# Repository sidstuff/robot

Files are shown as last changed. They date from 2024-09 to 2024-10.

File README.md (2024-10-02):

# Obstacle avoiding robot

A common type is the micromouse, a small robot which tries to solve a maze. I.e., it tries to reach the center of a maze made up of a 16×16 grid of cells, each 180 mm square with walls 50 mm high.

## Usage

Clone the repo and open with KiCAD.

## Schematic

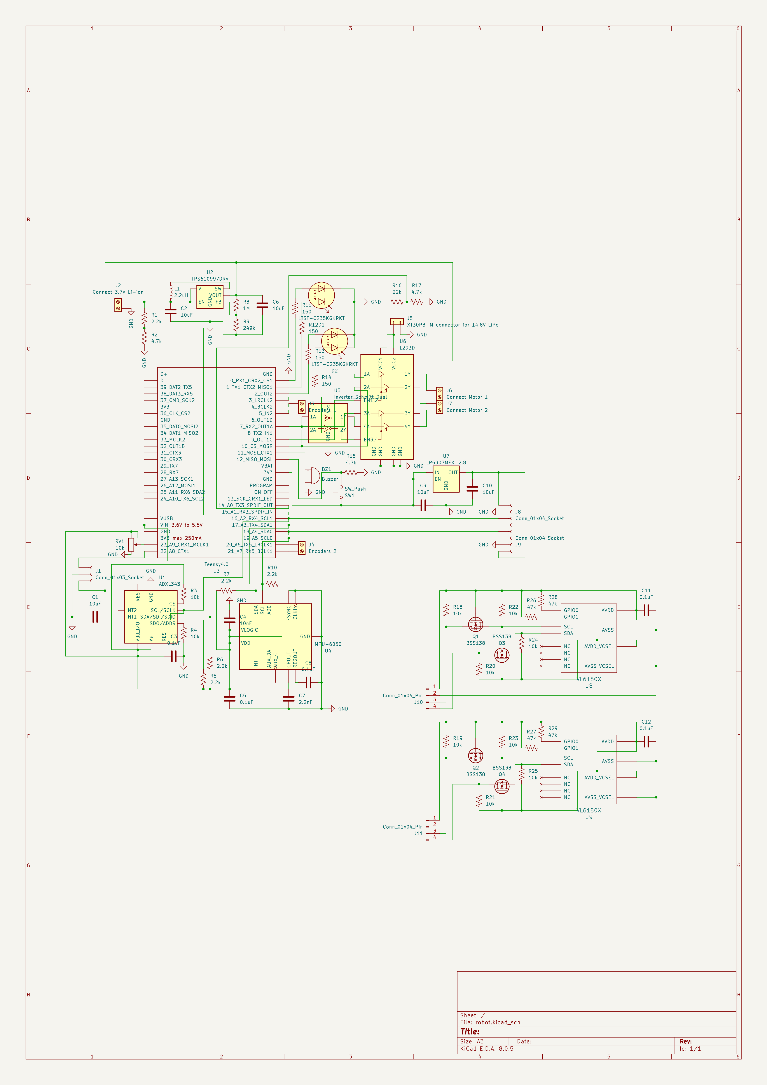
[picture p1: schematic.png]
Schematic


## Parts

While picking parts, ensure that the voltage/current/power ratings of componenets are not exceeded. Also, lithium cells have a nominal voltage of 3.7V (although it can go up to 4.2V when fully charged, and can be discharged until 3V), so their batteries are going to be multiples of the same.

### Microcontroller – Teensy 4.0

https://www.pjrc.com/store/teensy40.html

The Teensy 4.0 is compatible with the Arduino software, smaller than the Nano, and more powerful than the Giga (2x the CoreMark score). It needs a 5V supply voltage, so we'll use a 3.7V Li-ion battery with A TPS61099x 5V boost converter.

#### Why not older models?

> PJRC recommends use of Teensy 4.0 / 4.1 for new projects. We do not believe supply of chips for Teensy 3.x is likely to ever fully recover. These chips are made with 90 nm silicon process. Most of the world's semiconductor fabs are focusing on 45 nm or smaller, leaving limited supply for older chips. We anticipate the cost of these chips is likely to increase as the supply continues to dwindle.
>
> www.pjrc.com/store/teensylc.html

Thus we use the 4.x series to future-proof our design. The 4.0 is the smaller model of the series and is sufficient for our project.

### Motors – N20 gear motors, driven by the L293D

We will use the common N20 gear motor. To pick the specifications of the same, let's make use of this [Drive Motor Sizing Tool](https://community.robotshop.com/blog/show/drive-motor-sizing-tool)
```
Total mass: 210g                 When picking components, we should keep the total weight at or below this.
Number of drive motors: 2        Each of the rear wheels will have a sepaarte motor, turning will be achieved by driving them at different speeds.
Radius of drive wheel: 32.5 mm   Use 65 mm RC wheels
Robot velocity: 1.35 m/s         Micromice can run at over three meters per second, depending on the maze design.
Maximum incline: 0 deg           A simple maze solving robot doesn't need to worry about performance climbing inclines.
Supply voltage: 12 V             12V is the highest available voltage for the N20. A higher voltage means less current/charge is required for the same power/energy output. 
Desired acceleration: 4 m/s2     Micromice can run with forward acceleration and braking well over 1g.
Total efficiency: 40%            N20 motors have a maximum efficiency of around 0.4
```
```
Angular Velocity: 396.86 rpm
Torque: 0.34786 kgf-cm
Total Power: 1.4175 W
Maximum current: 118.13 mA
```
The [N20 motor rated for 12V 400RPM](https://robu.in/product/n20-12v-400-rpm-micro-metal-gear-motor) fulfils these requirements. It has a rated torque of 0.35 kg-cm. The recommendation for brushed DC motor operation is 25% or less of the stall current. The stall current for the above motor is 0.75 A, and the required current of 118.13 mA is less than 16% of it.

Make sure to buy the version with a [motor encoder](https://www.pololu.com/product/5215) and [its wires](https://www.pololu.com/product/4762) – it tells us how much the motor has rotated and thus the robot's speed as well as the distance travelled.

With these motors, we will use a pair of [65mm RC wheels](https://srituhobby.com/product/65mm-rubber-wheel-rc-model-tire).

On the [L293D motor driver](https://www.electronicscomp.com/l293d-dual-h-bridge-motor-driver-ic), there are two pins to control the direction of each motor as follows:
| IN1	| IN2 |	Spinning Direction |
| --- | --- | --- |
| LOW | LOW| Motor OFF |
| HIGH	| LOW | Forward |
| LOW | HIGH | Backward |
| HIGH	| HIGH |	Motor OFF |

The enable pin for each motor can be used to switch it on/off (as well as control the speed using PWM) so the `LOW,LOW` and `HIGH,HIGH` configurations are not needed. As for the remaining two, we can save two digital pins (one per motor) by using a logic inverter. Thus we use the Dual Schmitt-Trigger Inverter, but since we have a pin to spare, we end up using a digital pin for the inverter supply voltage (instead of the 3.3V pin) to simplify the connections.

The L293D will drop the motor supply voltage by ~2.6V, so we will use a 14.8V LiPo battery for the motors.

### Accelerometer – ADXL345

Calculating the position of the robot from the rotation of the motor is complicated by turns of the robot, and some slipping can mess up the entire calculation thereafter. Thus we make use of an accelerometer.

### Gyroscope - MPU6050

Similarly, a gyroscope tells us how many degrees the robot has turned.

<table><td><b>NOTE</b>: Both the ADXL345 and the MPU6050 are I2C devices and thus we use 2.2k pull-up resistors on the SDA and SCL connections because the Teensy's internal pull-up resistors are too weak.</td></table>

### Distance sensors

Note that distance sensors have a dead zone or blanking distance of say, x cm, beginning from the face of the sensor and extending outward, within which it cannot measure distances. One can simply position the sensor x cm inwards on the robot if they wish to measure distances in that zone.

#### Front - Sharp GP2Y0A41SK0F

https://www.pololu.com/product/2464

The GP2Y0A41SK0F is an IR sensor with a range of 4 – 30 cm. Considering the size of the robot and its enclosings, this is a good range within which to detect obstacles so the robot can decide if and how much to speed up, slow down, or stop, and can do so in time. A simple calculation is that if the robot is moving at its maximum speed of 1.35 m/s and has a maximum acceleration (deceleration in this case) of 4 m/s2, it can come to a stop within a distance of v²/2a = 22.8 cm.

This sensor draws current in large, short bursts, which is why we should (and do) place a 10 µF capacitor or larger across the 5V supply and ground, close to the sensor.

The sensor will be stuck to the front of the robot and a [3-Pin Female JST-PH Cable with male pins](https://www.pololu.com/product/1799) will be used to connect it to 0.1" female pins on our PCB.

#### Sides – VL6180X

https://www.pololu.com/product/2489

The sides of the robot will approach closer to walls and obstacles than the front, so a shorter minimum range is required. The VL6180X is a time-of-flight ranging sensor with a range of 1 – 20 cm (or 60 cm with reduced resolution), which is sufficient. It uses 2.8V logic, so we use the LP5907MFX-2.8 linear voltage regulator to convert 3.3V to 2.8V.

It is an I2C device, and we use 10k pull-up resistors on the SDA and SCL connections. Its I2C address will reset to 0x29 when powered off and on again, so for simplicity, we let the two chips have identical addresses and instead connect them to different SDA/SCL pins on the microcontroller.

Each chip (with its associated componenets) will be on a separate board that will be stuck to the side of the robot, and connected to the main PCB via common 0.1" pins and jumper cables.

### RG bicolor LEDs – LTST-C235KGKRKT

We use voltage dividers to supply a fraction of the two batteries' voltages to analog pins on the Teensy. Based on these, the microcontroller can make two corresponding bicolor LEDs display hues from green to yellow to red, to indicate the charge. An LED can blink red when the level is danngerously low, and blink green when its corresponding battery is done charging. The LED is rated for 20mA but the Teensy's pins have a limit of 10mA. The voltage supplied to the LED will always be 3.3V, the brightness will be controlled using PWM. The LED forward voltage is 2V. Thus the value of the current limiting resistor used should be at least (3.3−2)/0.01 = 130 ohms, so let's use a standard 150 ohm resistor.

### Buzzer – AI-3035-TWT-3V-R

We can have the buzzer buzz at different frequencies and beep at different delays to notify us of various things. Its rating of 3V,9mA is within the limits of the Teensy pin. For every doubling of distance, the sound level reduces by 6dB, so its volume of 100dB@10cm means that our buzzer will have a nicely audible volume of 60dB 10m away.

<table><td><b>TODO</b>: Due to laziness, the PCB currently uses KiCAD's standard 12x9.5mm buzzer footprint, which should be replaced with a custom but more accurate 30x20mm one – this means the PCB will be larger than it currently is.</td></table>

### Potentiometer – RK09K or similar

We'll use a 10k rotary potentiometer (vertical) with a knob to provide an analog voltage that indicates the speed at which we want the robot to move.

### Switches

We need two switches. First, an SPST rocker switch connected (not on the PCB) to the 3.7V battery to just switch on the circuitry, perhaps to check the working status of the components, battery level, etc. Then a normally open SPST Push button switch, like the MEC 5GTH935, to signal that the robot should start moving. Normally the Teensy pin is pulled down to ground, but when the switch is pressed, it momentarily becomes HIGH, and upon receiving this signal, the microcontroller starts the robot's motion.

### 2 Pin Screw Terminals – Xinya XY308-2P 2.54MM

In total, we require five [2 pin screw terminals](https://www.tme.com/in/en/details/xy308-2p-2.54-gn/pcb-terminal-blocks/xinya/xy308-2p-2-54mm-green) to connect various unterminated wires to the PCB.

### Batteries

| Part | Weight (g) | Voltage (V) | Current (mA) |
| --- | --- | --- | --- |
| 1 x Teensy 4.0 | 2.8 | 5 | 100 |
| 2 x N20 | 12 | 14.8 | 118 |
| 2 x wheels | 31 | - | - |
| 1 x L293D | 2.1 | 5 | 24 |
| 1 x ADXL345 | 0.03 | 3.3 | 0.04 |
| 1 x MPU6050 | 0.03 | 3.3 | 3.6 |
| 1 x GP2Y0A41SK0F | 3.5 | 5 | 12 |
| 2 x VL6180X (with LP5907MFX) | 0.03 | 3.3 | 25 |
| 2 x (LTST-C235KGKRKT + 150ohm) | 0.04 | 3.3 | 8.67 |
| 1 x AI-3035-TWT-3V-R | 12 | 3 | 9* |
| 1 x RK09K | 4.5 | 3.3 | 0.33 |
| 1 x Rocker Switch | 1.4 | 0 | - |
| 1 x 5GTH935 | 3 | 3.3 | 0.7* |
| 5 x XY308-2.54 | 0.5 | 0 | - |

`*` – current flows rarely

Adding all the weights, we get 112g. For the batteries, let's pick the [3.7V 3.7Wh 1000mAh LiPo](https://www.lithium-polymer-battery.net/lp543450-3-7v-1000mah-3-7wh-lithium-polymer-battery)  (20g) and the [Orange 14.8V 360mAh 25C 4S LiPo](https://robu.in/product/orange-360mah-4s-25c-14-8-v-lithium-polymer-battery-pack-li-po) (60g). This brings the weight up to 192g, but this is excluding the PCB material, wires, connectors, and small circuit elements. A PCB weighs a couple grams per square inch – see [custompcb.com/faq.php](https://custompcb.com/faq.php) – so the final weight should come out to around 210g.

The 14.8V Lipo is 25C, so can deliver a maximum current of 0.36Ah * 25h^(-1) = 9A, which is more than enough for our motors. They draw upto 2 * 118mA = 236 mA, so our battery will last 360mAh / 236 mA = 1.5h, if the robot was continuously running at full power, but in reality, will last longer.

The following diagram shows the flow of current from the 3.7V LiPo.
```
------------------------------------ 3.7V
               |
      301.2 mA (1114.5 mW)
               |
      ----------------------
      | TPS61099 (93% eff) |
      ----------------------
               |
---------------|-------------------- 5V
               |
      207.3 mA (1036.5 mW)
               |
      -------------------
      |                 |
      |              171.3 mA
      |                 |
 --------------  -------|------------------
 | 5V Devices |  |      |                 |
 --------------  |  ----------            |
      |          |  | Teensy |            |
      |          |  ----------            |
    36 mA        |   |      |             |
      |          |   |   ---|--- 3.3V     |
      |          | 100mA    |             |
      |          |   |   ---------------- |
      |          |   |   | 3.3V Devices | |
      |          |   |   ---------------- |
      |          |   |      |             |
      |          ----|------|--------------
      |              |      |
      |              |    71.3 mA
      |              |      |
      V              V      V
------------------------------------ GND
```

The 3.7V LiPo has a max continuous discharge current of 1000 mA so it will be able to provide our required current of 301.2 mA. It is a 3.7 Wh battery, so it will last 3.7Wh/1114.5mW = 3.3h.

## PCB

For a 1 oz copper thickness PCB, KiCAD's default trace width of 0.200mm is sufficient for the amount of current in our circuit, and so are the default 0.6/0.3 mm vias. We must also make sure to maintain some clearance betweeen traces, to prevent crosstalk. The routing in our PCB is tight at places, which is why our ground plane is important in that it reduces crosstalk.

From Wikipedia:
>  When two traces run parallel, an electrical signal in one can be coupled into the other through electromagnetic induction by magnetic field lines from one linking the other; this is called crosstalk. When a ground plane layer is present underneath, it forms a transmission line with the trace. The oppositely-directed return currents flow through the ground plane directly beneath the trace. This confines most of the electromagnetic fields to the area near the trace and consequently reduces crosstalk.

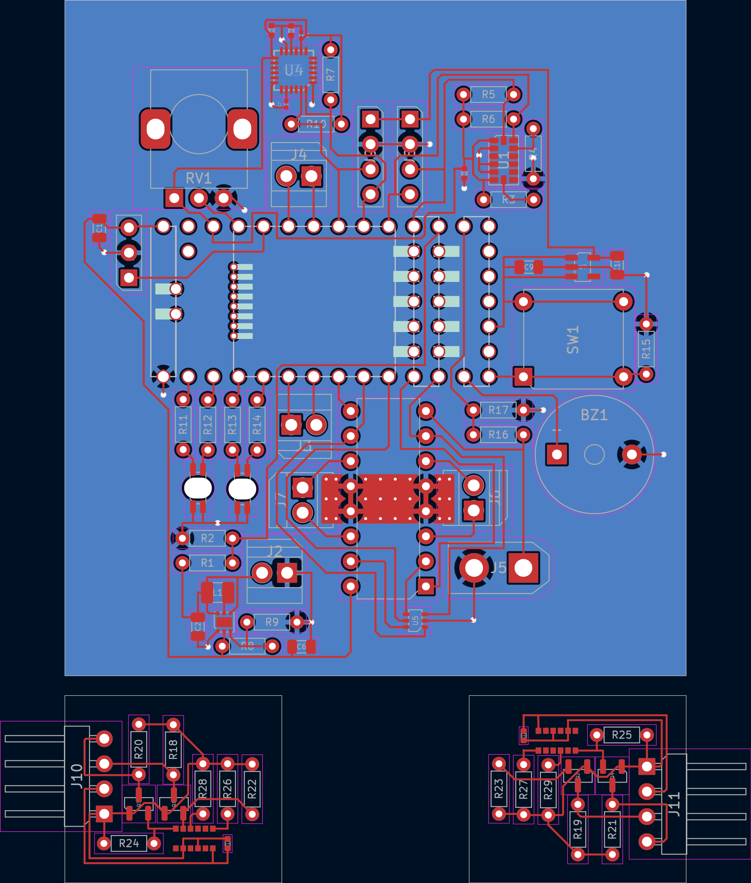
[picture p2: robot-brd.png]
Footprint

<br>
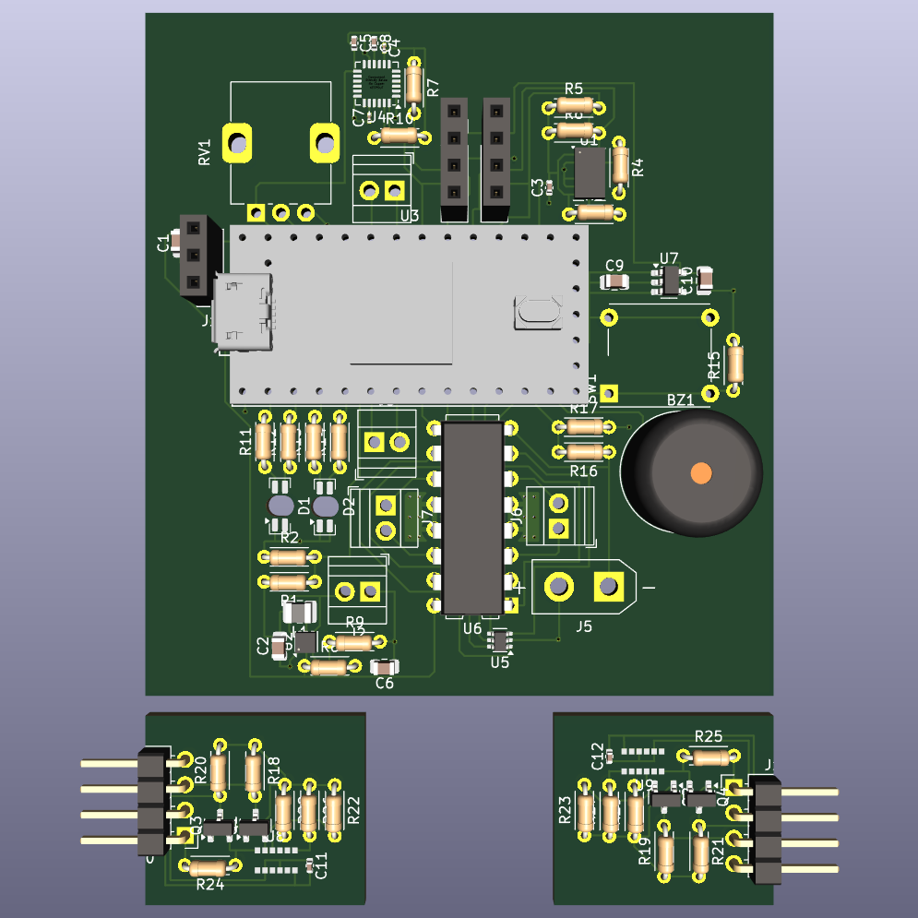
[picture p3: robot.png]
3D View


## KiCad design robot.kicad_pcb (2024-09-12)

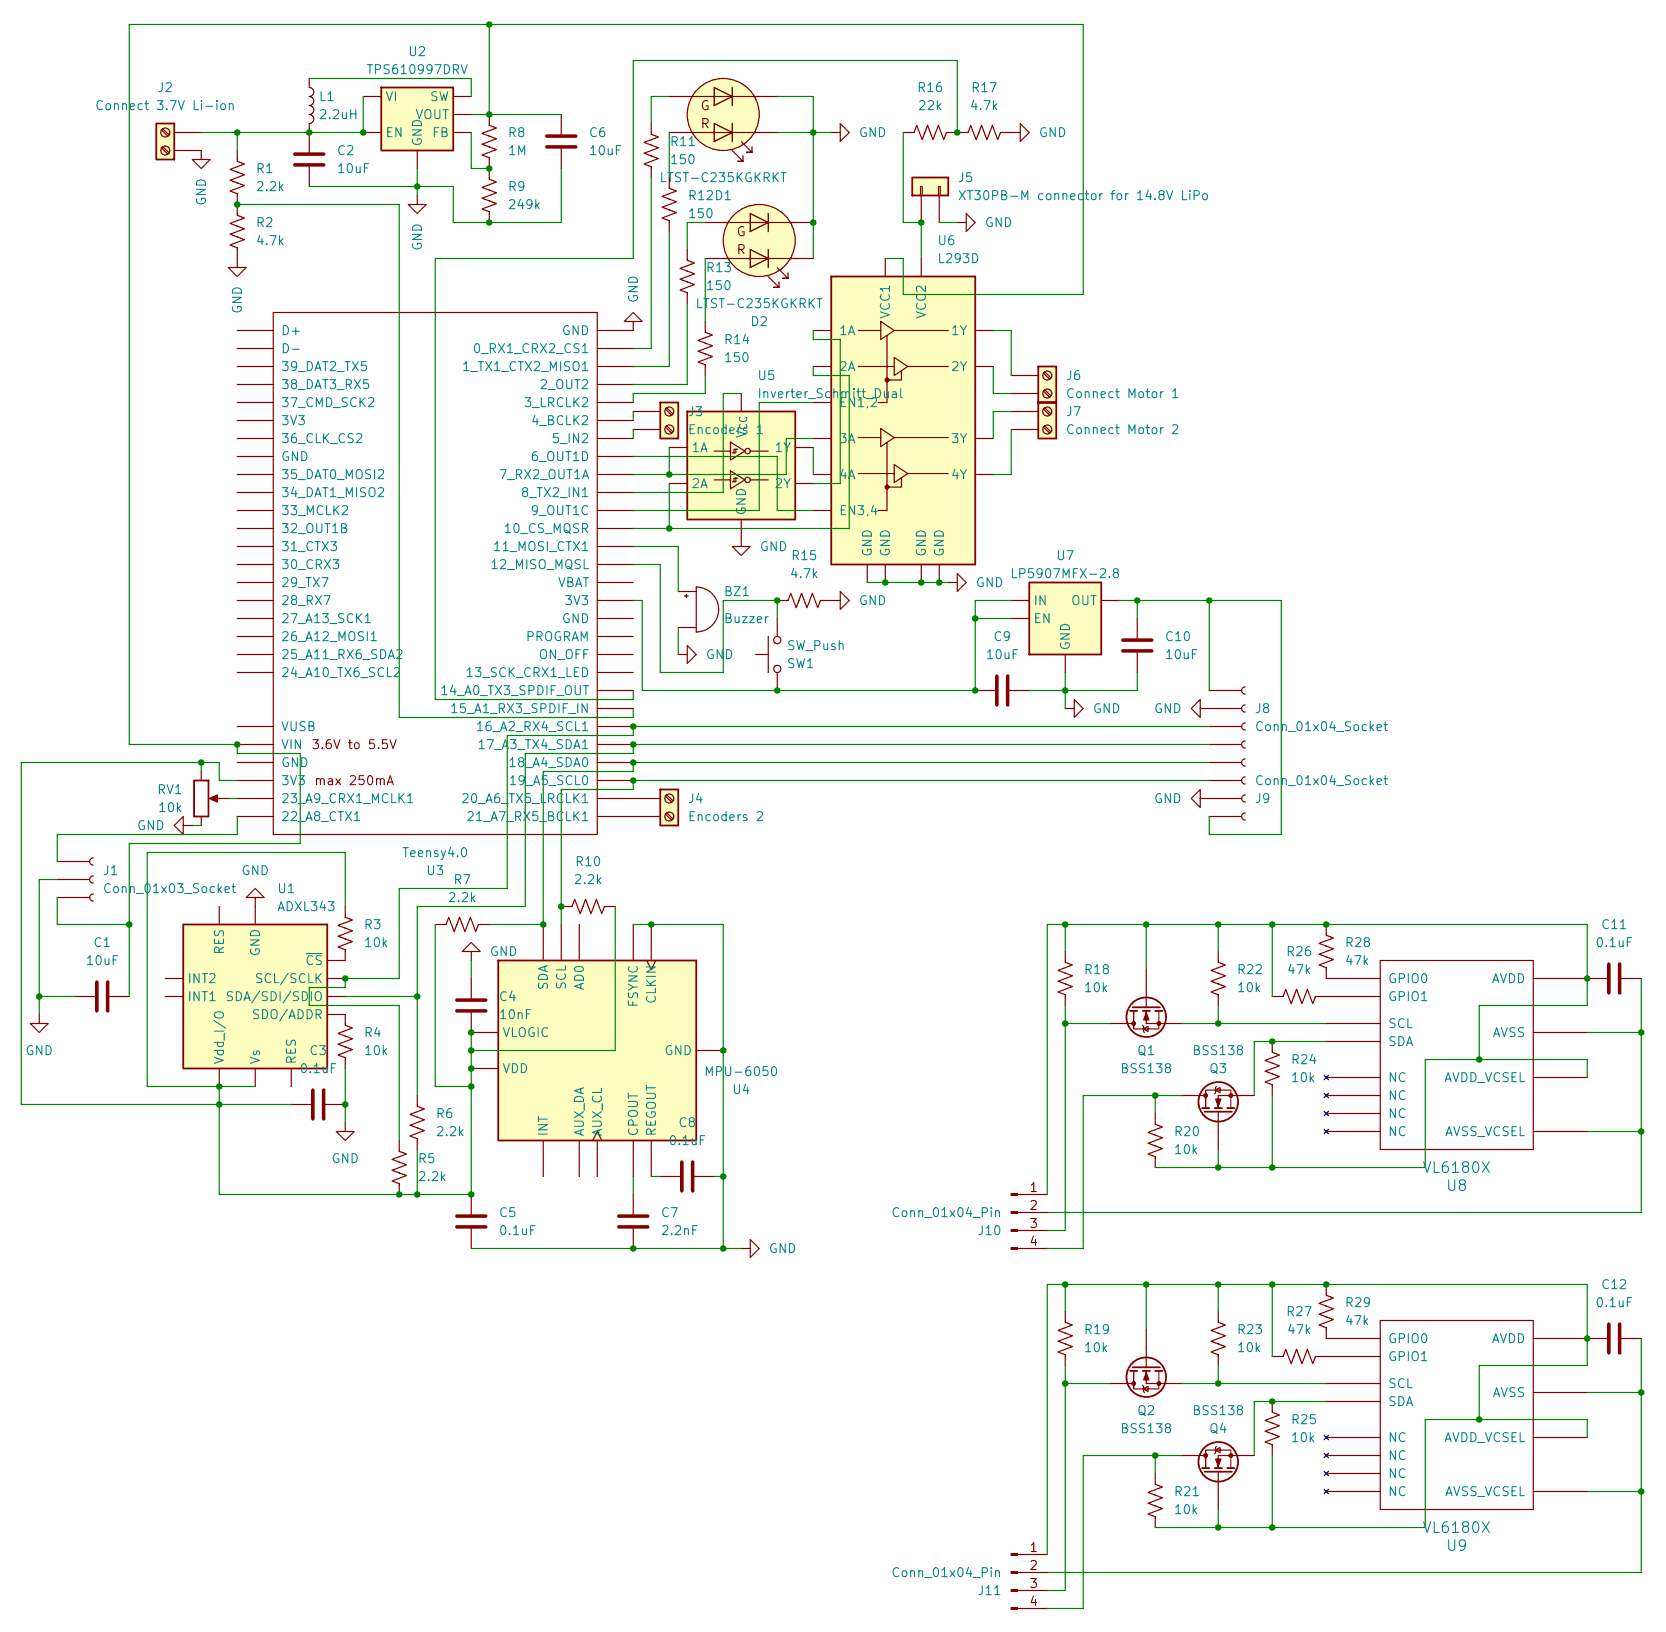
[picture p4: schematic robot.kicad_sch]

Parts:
BZ1: Buzzer; Buzzer_12x9.5RM7.6
C1, C2, C6, C9, C10: 10uF; C_0805_2012Metric
C3, C5, C8, C11, C12: 0.1uF; C_0402_1005Metric
C4: 10nF; C_0201_0603Metric
C7: 2.2nF; C_0201_0603Metric
D1, D2: LTST-C235KGKRKT; LED_LiteOn_LTST-C235KGKRKT
J1: Conn_01x03_Socket; PinSocket_1x03_P2.54mm_Vertical
J2: Connect 3.7V Li-ion; TerminalBlock_Xinya_XY308-2.54-2P_1x02_P2.54mm_Horizontal
J3: Encoders 1; TerminalBlock_Xinya_XY308-2.54-2P_1x02_P2.54mm_Horizontal
J4: Encoders 2; TerminalBlock_Xinya_XY308-2.54-2P_1x02_P2.54mm_Horizontal
J5: XT30PB-M connector for 14.8V LiPo; AMASS_XT30UPB-M_1x02_P5.0mm_Vertical
J6: Connect Motor 1; TerminalBlock_Xinya_XY308-2.54-2P_1x02_P2.54mm_Horizontal
J7: Connect Motor 2; TerminalBlock_Xinya_XY308-2.54-2P_1x02_P2.54mm_Horizontal
J8, J9: Conn_01x04_Socket; PinSocket_1x04_P2.54mm_Vertical
J10, J11: Conn_01x04_Pin; PinHeader_1x04_P2.54mm_Horizontal
L1: 2.2uH; L_1008_2520Metric
Q1, Q2, Q3, Q4: BSS138; SOT-23
R1, R5, R6, R7, R10: 2.2k; R_Axial_DIN0204_L3.6mm_D1.6mm_P5.08mm_Horizontal
R2, R15, R17: 4.7k; R_Axial_DIN0204_L3.6mm_D1.6mm_P5.08mm_Horizontal
R3, R4, R18, R19, R20, R21, R22, R23, R24, R25: 10k; R_Axial_DIN0204_L3.6mm_D1.6mm_P5.08mm_Horizontal
R8: 1M; R_Axial_DIN0204_L3.6mm_D1.6mm_P5.08mm_Horizontal
R9: 249k; R_Axial_DIN0204_L3.6mm_D1.6mm_P5.08mm_Horizontal
R11, R12, R13, R14: 150; R_Axial_DIN0204_L3.6mm_D1.6mm_P5.08mm_Horizontal
R16: 22k; R_Axial_DIN0204_L3.6mm_D1.6mm_P5.08mm_Horizontal
R26, R27, R28, R29: 47k; R_Axial_DIN0204_L3.6mm_D1.6mm_P5.08mm_Horizontal
RV1: 10k; Potentiometer_Alps_RK09K_Single_Vertical
SW1: SW_Push; SW_MEC_5GTH9
U1: ADXL343; LGA-14_3x5mm_P0.8mm_LayoutBorder1x6y
U2: TPS610997DRV; WSON-6-1EP_2x2mm_P0.65mm_EP1x1.6mm
U3: Teensy4.0; Teensy40_SMT
U4: MPU-6050; InvenSense_QFN-24_4x4mm_P0.5mm
U5: Inverter_Schmitt_Dual; SOT-363_SC-70-6
U6: L293D; DIP-16_W7.62mm
U7: LP5907MFX-2.8; SOT-23-5
U8, U9: VL6180X

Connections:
GND: BZ1.2 (-), C1.1, C2.1, C3.1, C4.1, C5.1, C6.1, C7.1, C8.1, C9.2, C10.1, D1.1 (K2), D1.4 (K1), D2.1 (K2), D2.4 (K1), J1.2, J2.1, J5.2, J8.2, J9.2, R2.1, R4.2, R9.2, R15.2, R17.2, RV1.3, U1.2 (GND), U1.4 (GND), U1.5 (GND), U2.1 (GND), U2.7 (GND), U3.1 (GND), U4.1 (CLKIN), U4.11 (FSYNC), U4.18 (GND), U5.2 (GND), U6.4 (GND), U6.5 (GND), U6.12 (GND), U6.13 (GND), U7.2 (GND)
unnamed: BZ1.1 (+), U3.13 (11_MOSI_CTX1)
unnamed: D1.3 (A1), R12.1
unnamed: D1.2 (A2), R11.1
unnamed: D2.3 (A1), R14.1
unnamed: D2.2 (A2), R13.1
unnamed: J1.1, U3.29 (22_A8_CTX1)
unnamed: C1.2, C6.2, J1.3, R8.1, U2.2 (VOUT), U3.33 (VIN), U6.16 (VCC1)
unnamed: C2.2, J2.2, L1.2, R1.2, U2.4 (EN), U2.6 (VI)
unnamed: J3.1, U3.6 (4_BCLK2)
unnamed: J3.2, U3.7 (5_IN2)
unnamed: J4.1, U3.27 (20_A6_TX5_LRCLK1)
unnamed: J4.2, U3.28 (21_A7_RX5_BCLK1)
unnamed: J5.1, R16.1, U6.8 (VCC2)
unnamed: J6.1, U6.3 (1Y)
unnamed: J6.2, U6.6 (2Y)
unnamed: J7.1, U6.11 (3Y)
unnamed: J7.2, U6.14 (4Y)
unnamed: C10.2, J8.1, J9.1, U7.5 (OUT)
unnamed: J8.3, R5.2, U1.14 (SCL/SCLK), U3.23 (16_A2_RX4_SCL1)
unnamed: J8.4, R6.2, U1.13 (SDA/SDI/SDIO), U3.24 (17_A3_TX4_SDA1)
unnamed: J9.3, R10.1, U3.26 (19_A5_SCL0), U4.23 (SCL)
unnamed: J9.4, R7.2, U3.25 (18_A4_SDA0), U4.24 (SDA)
unnamed: C11.1, J10.1, Q1.1 (G), Q3.1 (G), R18.1, R20.2, R22.1, R24.2, R26.1, R28.1, U8.8 (AVDD_VCSEL), U8.10 (AVDD)
unnamed: C11.2, J10.2, U8.9 (AVSS_VCSEL), U8.12 (AVSS)
unnamed: J10.3, Q1.3 (D), R18.2
unnamed: J10.4, Q3.3 (D), R20.1
unnamed: C12.1, J11.1, Q2.1 (G), Q4.1 (G), R19.1, R21.2, R23.1, R25.2, R27.1, R29.1, U9.8 (AVDD_VCSEL), U9.10 (AVDD)
unnamed: C12.2, J11.2, U9.9 (AVSS_VCSEL), U9.12 (AVSS)
unnamed: J11.3, Q2.3 (D), R19.2
unnamed: J11.4, Q4.3 (D), R21.1
unnamed: Q1.2 (S), R22.2, U8.5 (SCL)
unnamed: Q2.2 (S), R23.2, U9.5 (SCL)
unnamed: Q3.2 (S), R24.1, U8.6 (SDA)
unnamed: Q4.2 (S), R25.1, U9.6 (SDA)
unnamed: R4.1, U1.12 (SDO/ADDR)
unnamed: C3.2, C4.2, C5.2, R3.1, R5.1, R6.1, R7.1, R10.2, RV1.1, U1.1 (Vdd_I/O), U1.6 (Vs), U3.31 (3V3), U4.8 (VLOGIC), U4.13 (VDD)
unnamed: R3.2, U1.7 (~CS)
unnamed: R8.2, R9.1, U2.3 (FB)
unnamed: L1.1, U2.5 (SW)
unnamed: R11.2, U3.2 (0_RX1_CRX2_CS1)
unnamed: R12.2, U3.3 (1_TX1_CTX2_MISO1)
unnamed: R13.2, U3.4 (2_OUT2)
unnamed: R14.2, U3.5 (3_LRCLK2)
unnamed: U3.8 (6_OUT1D), U6.9 (EN3,4)
unnamed: U3.9 (7_RX2_OUT1A), U5.1 (1A), U6.10 (3A)
unnamed: U3.10 (8_TX2_IN1), U5.5 (V_{CC})
unnamed: U3.11 (9_OUT1C), U6.1 (EN1,2)
unnamed: U3.12 (10_CS_MQSR), U5.3 (2A), U6.7 (2A)
unnamed: R15.1, SW1.1, U3.14 (12_MISO_MQSL)
unnamed: R16.2, R17.1, U3.21 (14_A0_TX3_SPDIF_OUT)
unnamed: R1.1, R2.2, U3.22 (15_A1_RX3_SPDIF_IN)
unnamed: RV1.2, U3.30 (23_A9_CRX1_MCLK1)
unnamed: C7.2, U4.20 (CPOUT)
unnamed: C8.2, U4.10 (REGOUT)
unnamed: U5.6 (1Y), U6.15 (4A)
unnamed: U5.4 (2Y), U6.2 (1A)
unnamed: C9.1, SW1.2, U3.16 (3V3), U7.1 (IN), U7.3 (EN)
unnamed: R28.2, U8.4 (GPIO0)
unnamed: R26.2, U8.1 (GPIO1)
unnamed: R29.2, U9.4 (GPIO0)
unnamed: R27.2, U9.1 (GPIO1)

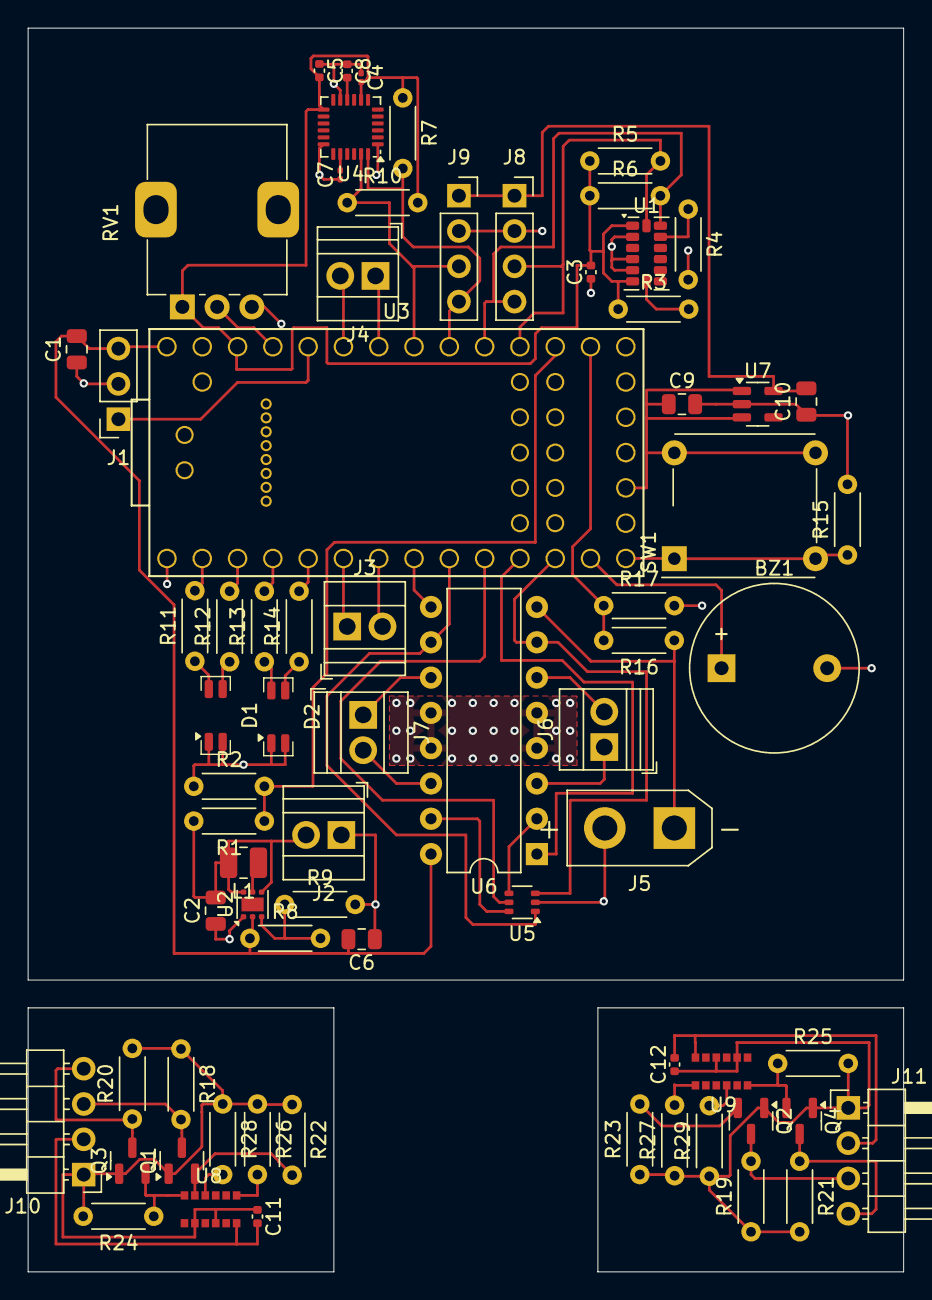
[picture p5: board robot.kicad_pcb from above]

Board: 2 copper layers, 63.0 x 89.5 mm, 71 parts (0 on the bottom side), 62 nets.
